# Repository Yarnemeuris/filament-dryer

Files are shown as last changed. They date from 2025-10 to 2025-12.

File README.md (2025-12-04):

# filament-dryer
A simple filament dryer for drying 1 kg spools of filament. It's based around an Ender 3 heater and fan, combined with a PCB and another sensor. All controlled via Klipper. More information on CAD, firmware and the PCB is available in the folders.

CAD model

## CAD
The filament is made for 3D printing and it will use about 350g of ABS/ASA. I deigned it in onshape, here is the [link](https://cad.onshape.com/documents/1bd024d5b7959acafc85207a/w/bc3f431890b8dcf2703dc2b2/e/cdbebe0165cb72dab1a66bad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) if you want to see it yourself. Here are some more pictures from onshape:

electronics
side view
open

## PCB
It uses a custom 2 layer pcb, that's designed to be hand soldered. Most of the components are through hole and the one that isn't is pretty zasy to do yourself. Here are some pictures of the pcb:

PCB 3D model
PCB
schematic

## BOM
In the BOM it uses a pico W because that is the only one LCSC has. You could also use a normal pico, but then you will need to get it from somewhere else.

| Category | Item | Quantity | Minimum Order Quantity | Unit Price | Total Price | URL | Running Total |
| ---: | ---: | ---: | ---: | ---: | ---: | ---: | ---: |
| PCB Components | Capacitor 10µF | 1 | 1 |  $ 0.3996  | $0.40 | https://www.lcsc.com/product-detail/C531341.html |  $ 0.40  |
| PCB Components | Capacitor 22µF | 1 | 1 |  $ 1.2269  | $1.23 | https://www.lcsc.com/product-detail/C531341.html |  $ 1.63  |
| PCB Components | JST XH connector | 5 | 10 |  $ 0.0482  | $0.48 | https://www.lcsc.com/product-detail/C378939.html |  $ 2.11  |
| PCB Components | Screw Terminal | 2 | 5 |  $ 0.1102  | $0.55 | https://www.lcsc.com/product-detail/C8465.html |  $ 2.66  |
| PCB Components | Mosfet | 2 | 1 |  $ 0.8775  | $1.76 | https://www.lcsc.com/product-detail/C38774.html |  $ 4.41  |
| PCB Components | Resistor 100Ω | 2 | 50 |  $ 0.0110  | $0.55 | https://www.lcsc.com/product-detail/C120214.html |  $ 4.96  |
| PCB Components | Resistor 100KΩ | 2 | 20 |  $ 0.0242  | $0.48 | https://www.lcsc.com/product-detail/C119444.html |  $ 5.45  |
| PCB Components | Resistor 120Ω | 1 | 20 |  $ 0.0122  | $0.24 | https://www.lcsc.com/product-detail/C359996.html |  $ 5.69  |
| PCB Components | Resistor 7KΩ | 1 | 20 |  $ 0.0229  | $0.46 | https://www.lcsc.com/product-detail/C119429.html |  $ 6.15  |
| PCB Components | CAN Transceiver | 1 | 1 |  $ 2.6161  | $2.62 | https://www.lcsc.com/product-detail/C16468.html |  $ 8.77  |
| PCB Components | Voltage Regulator | 1 | 1 |  $ 3.5895  | $3.59 | https://www.lcsc.com/product-detail/C22371890.html |  $ 12.36  |
| PCB Components | Jumper | 1 | 5 |  $ 0.0880  | $0.44 | https://www.lcsc.com/product-detail/C265313.html |  $ 12.80  |
| PCB Components | AHT21 Sensor | 1 | 1 |  $ 1.5105  | $1.51 | https://www.lcsc.com/product-detail/C3012624.html |  $ 14.31  |
| PCB Components | Pico W | 1 | 1 |  $ 10.7204  | $10.72 | https://www.lcsc.com/product-detail/C7203003.html |  $ 25.03  |
| PCB Components | 1x20 Pin Header | 2 | 5 |  $ 0.0566  | $0.28 | https://www.lcsc.com/product-detail/C42431804.html |  $ 25.31  |
| PCB Components | LCSC Shipping lcsc shipping | 1 |  |  $ 10.88  | $10.88 |  |  $ 36.19  |
| PCB | PCB (incl. shipping) jlcpcb shipping | 1 | 1 |  $ 4.24  | $4.24 | https://jlcpcb.com/ |  $ 40.43  |
| Parts | Heater | 1 |  | (from Ender 3) |  |  |  $ 40.43  |
| Parts | 4010 Blower Fan | 1 |  | (from Ender 3) |  |  |  $ 40.43  |
| Case | Printed Parts | 350g |  |  (I already own)  |  |  |  $ 40.43  |
| Case | Screws M3x12 | 4 |  |  (I already own)  |  |  |  $ 40.43  |
| Case | Screws M3x8 | 2 |  |  (I already own)  |  |  |  $ 40.43  |
| Case | Screws M3x16 | 2 |  |  (I already own)  |  |  |  $ 40.43  |
| Case | M3 Nuts | 6 |  |  (I already own)  |  |  |  $ 40.43  |
| Case | voron inserts | 2 |  |  (I already own)  |  |  |  $ 40.43  |

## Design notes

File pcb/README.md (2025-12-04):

# PCB
The filament dryer uses a custom 2 layer pcb. I made it with almost only through hole components, so you don't need to order PCBA. But make sure when you order on both JLCPCB and LCSC that you chose global standard direct line. It is the cheapest option and bad things will happend if you don't. All the files needed for the pcb production and parts are in de production folder. The zip is the gerber files for JLCPCB and you can upload the bom.csv to LCSC. But add the extra sensor, pico and headers to your cart as well.

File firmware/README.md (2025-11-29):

# Firmware

Here you can find the Klipper config. The firmware for the Pico itself can be obtained via Klipper itself. It should have the default settings, but communication is via CANbus with RX on pin 4 and TX on pin 5.

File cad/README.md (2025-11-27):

# CAD
There is a step file with the whole filament dryer in it, including the PCB and not printed components. You can also visit the [Onshape document](https://cad.onshape.com/documents/1bd024d5b7959acafc85207a/w/bc3f431890b8dcf2703dc2b2/e/cdbebe0165cb72dab1a66bad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), to view it and how I made it for yourself.

I have also included an STL file for each part to print. Which are orientated how I think you should print them (some have long bridges).

Lastly, there is also an OrcaSlicer 3MF file with the exact settings I used to print it.

## Print Settings
I don't have much to say here. I would recommend printing it from ABS or ASA, because it will get hot and PLA will melt. I used settings that aren't very strong but save filament. But it still is like 400 g.

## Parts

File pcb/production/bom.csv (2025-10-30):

Designator | Footprint | Quantity | Value | LCSC Part #
A1 | RaspberryPi_Pico_Common_THT | 1 | RaspberryPi_Pico
C1 | C_Disc_D6.0mm_W4.4mm_P5.00mm | 1 | 10µF | C531341
C2 | C_Disc_D6.0mm_W4.4mm_P5.00mm | 1 | 22µF | C5259863
J1, J3, J4, J5, J7 | JST_XH_B2B-XH-A_1x02_P2.50mm_Vertical | 5 | Conn_01x02 | C378939
J2, J6 | TerminalBlock_CUI_TB007-508-02_1x02_P5.08mm_Horizontal | 2 | Screw_Terminal | C8465
Q1, Q2 | TO-220-3_Horizontal_TabDown | 2 | IRLZ44N | C38774
R1, R2 | R_Axial_DIN0309_L9.0mm_D3.2mm_P12.70mm_Horizontal | 2 | 100Ω | C120214
R3, R4 | R_Axial_DIN0309_L9.0mm_D3.2mm_P12.70mm_Horizontal | 2 | 100KΩ | C119444
R6 | R_Axial_DIN0309_L9.0mm_D3.2mm_P12.70mm_Horizontal | 1 | 120Ω | C359996
R7 | R_Axial_DIN0309_L9.0mm_D3.2mm_P12.70mm_Horizontal | 1 | 4.7KΩ | C119429
U1 | SOIC-8_3.9x4.9mm_P1.27mm | 1 | SN65HVD230 | C16468
U2 | Converter_DCDC_RECOM_R-78E-0.5_THT | 1 | R-78E5.0-1.0 | C22371890

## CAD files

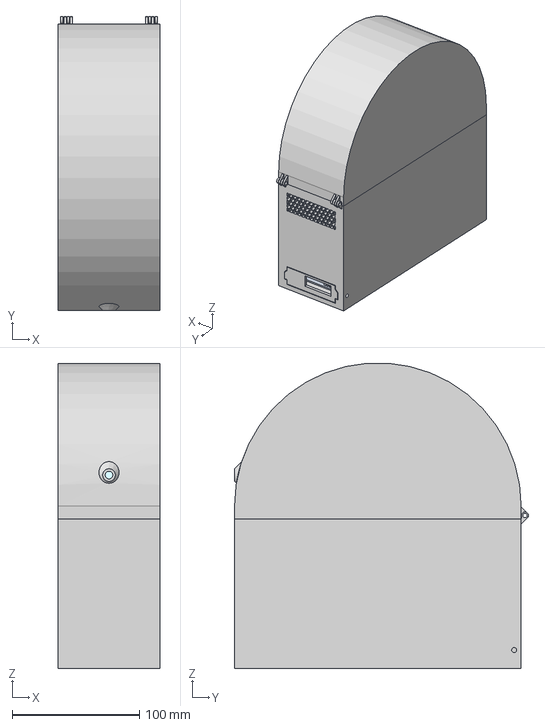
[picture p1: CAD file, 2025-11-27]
cad/filament dryer.step
80.0 x 230.7 x 239.7 mm

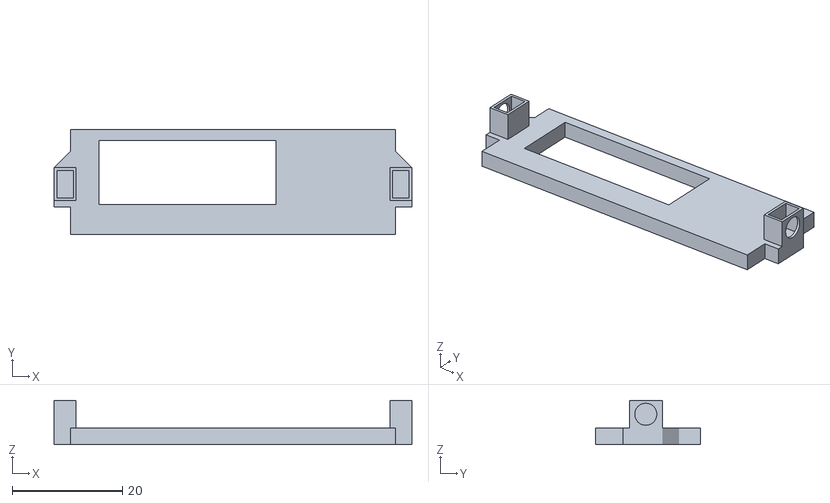
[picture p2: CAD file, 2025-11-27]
cad/STLs/backdoor.stl
65.0 x 19.0 x 8.00

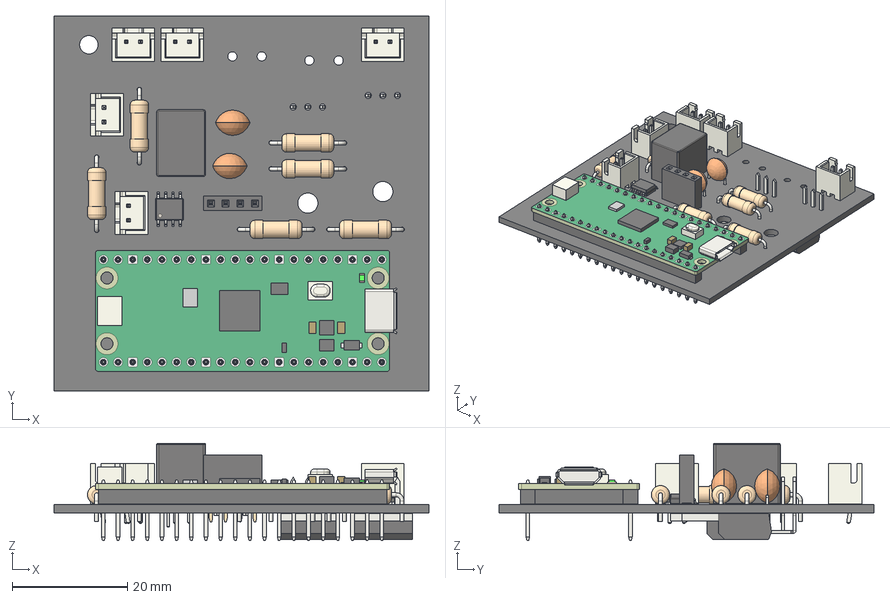
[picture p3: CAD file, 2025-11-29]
pcb/filament dryer.step
65.0 x 65.0 x 16.9 mm
C_Disc_D6.0mm_W4.4mm_P5.00mm x 2
SOIC-8_3.9x4.9mm_P1.27mm
R_Axial_DIN0309_L9.0mm_D3.2mm_P12.70mm_Horizontal x 6
JST_XH_B2B-XH-A_1x02_P2.50mm_Vertical x 5
RaspberryPi_Pico_H_Module_KiCad
RaspberryPi_Pico_Header_DIP-40_H2.54mm_KiCad
PinSocket_1x04_P2.54mm_Vertical
Converter_DCDC_RECOM_R-78E-0.5_THT
TO-220-3_Horizontal_TabDown x 2
filament dryer_PCB

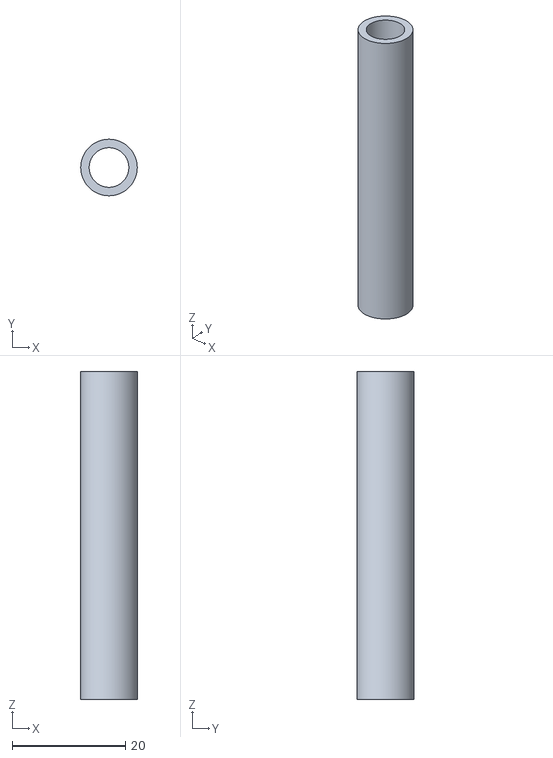
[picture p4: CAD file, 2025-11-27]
cad/STLs/2x_roller.stl
10.00 x 10.00 x 58.0

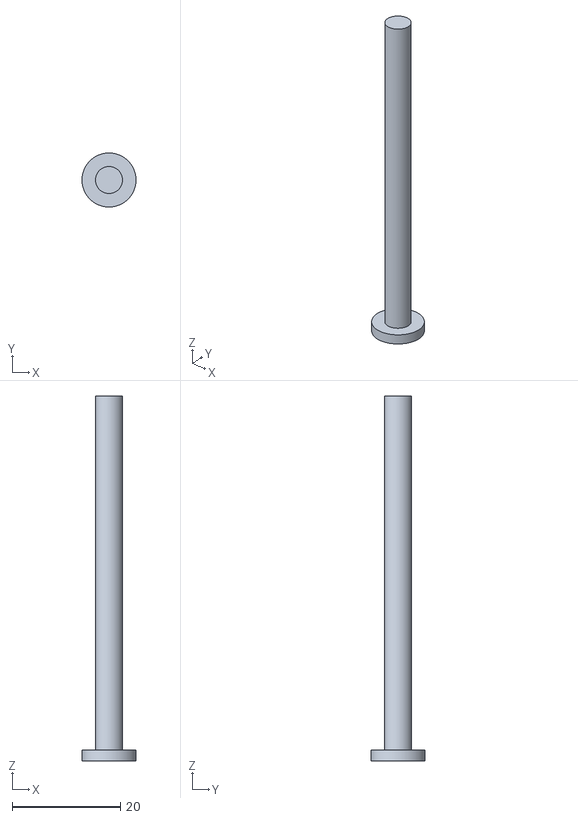
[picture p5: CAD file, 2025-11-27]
cad/STLs/2x_roller_pin.stl
10.00 x 10.00 x 67.5

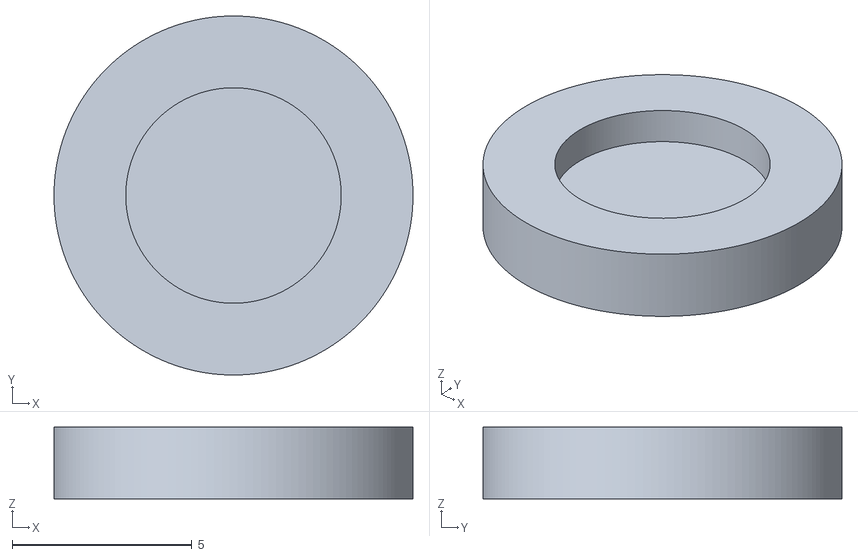
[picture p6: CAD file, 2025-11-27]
cad/STLs/2x_roller_cap.stl
10.00 x 10.00 x 2.00

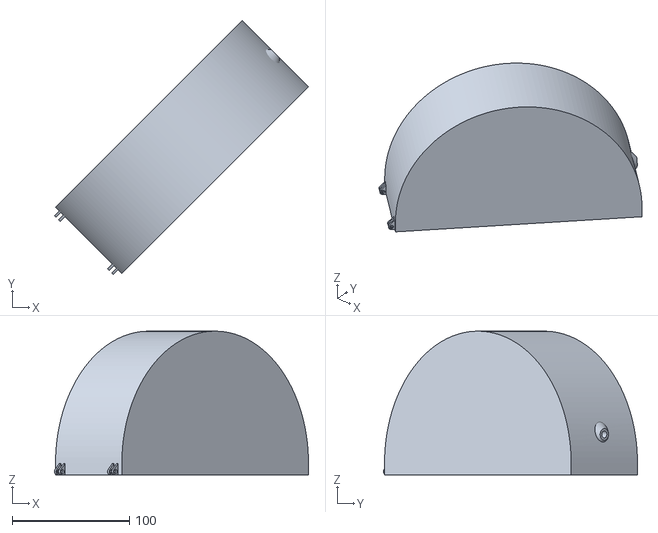
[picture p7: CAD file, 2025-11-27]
cad/STLs/top.stl
216.5 x 216.5 x 122.5

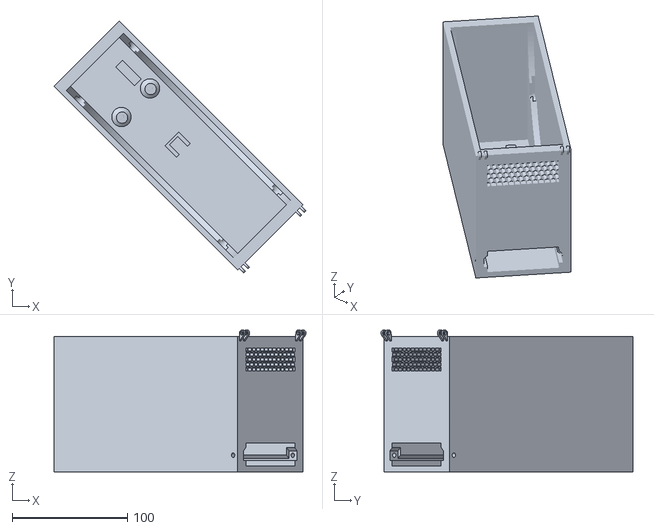
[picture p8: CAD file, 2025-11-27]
cad/STLs/bottom.stl
218.3 x 218.3 x 123.0

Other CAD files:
cad/filament dryer.3mf

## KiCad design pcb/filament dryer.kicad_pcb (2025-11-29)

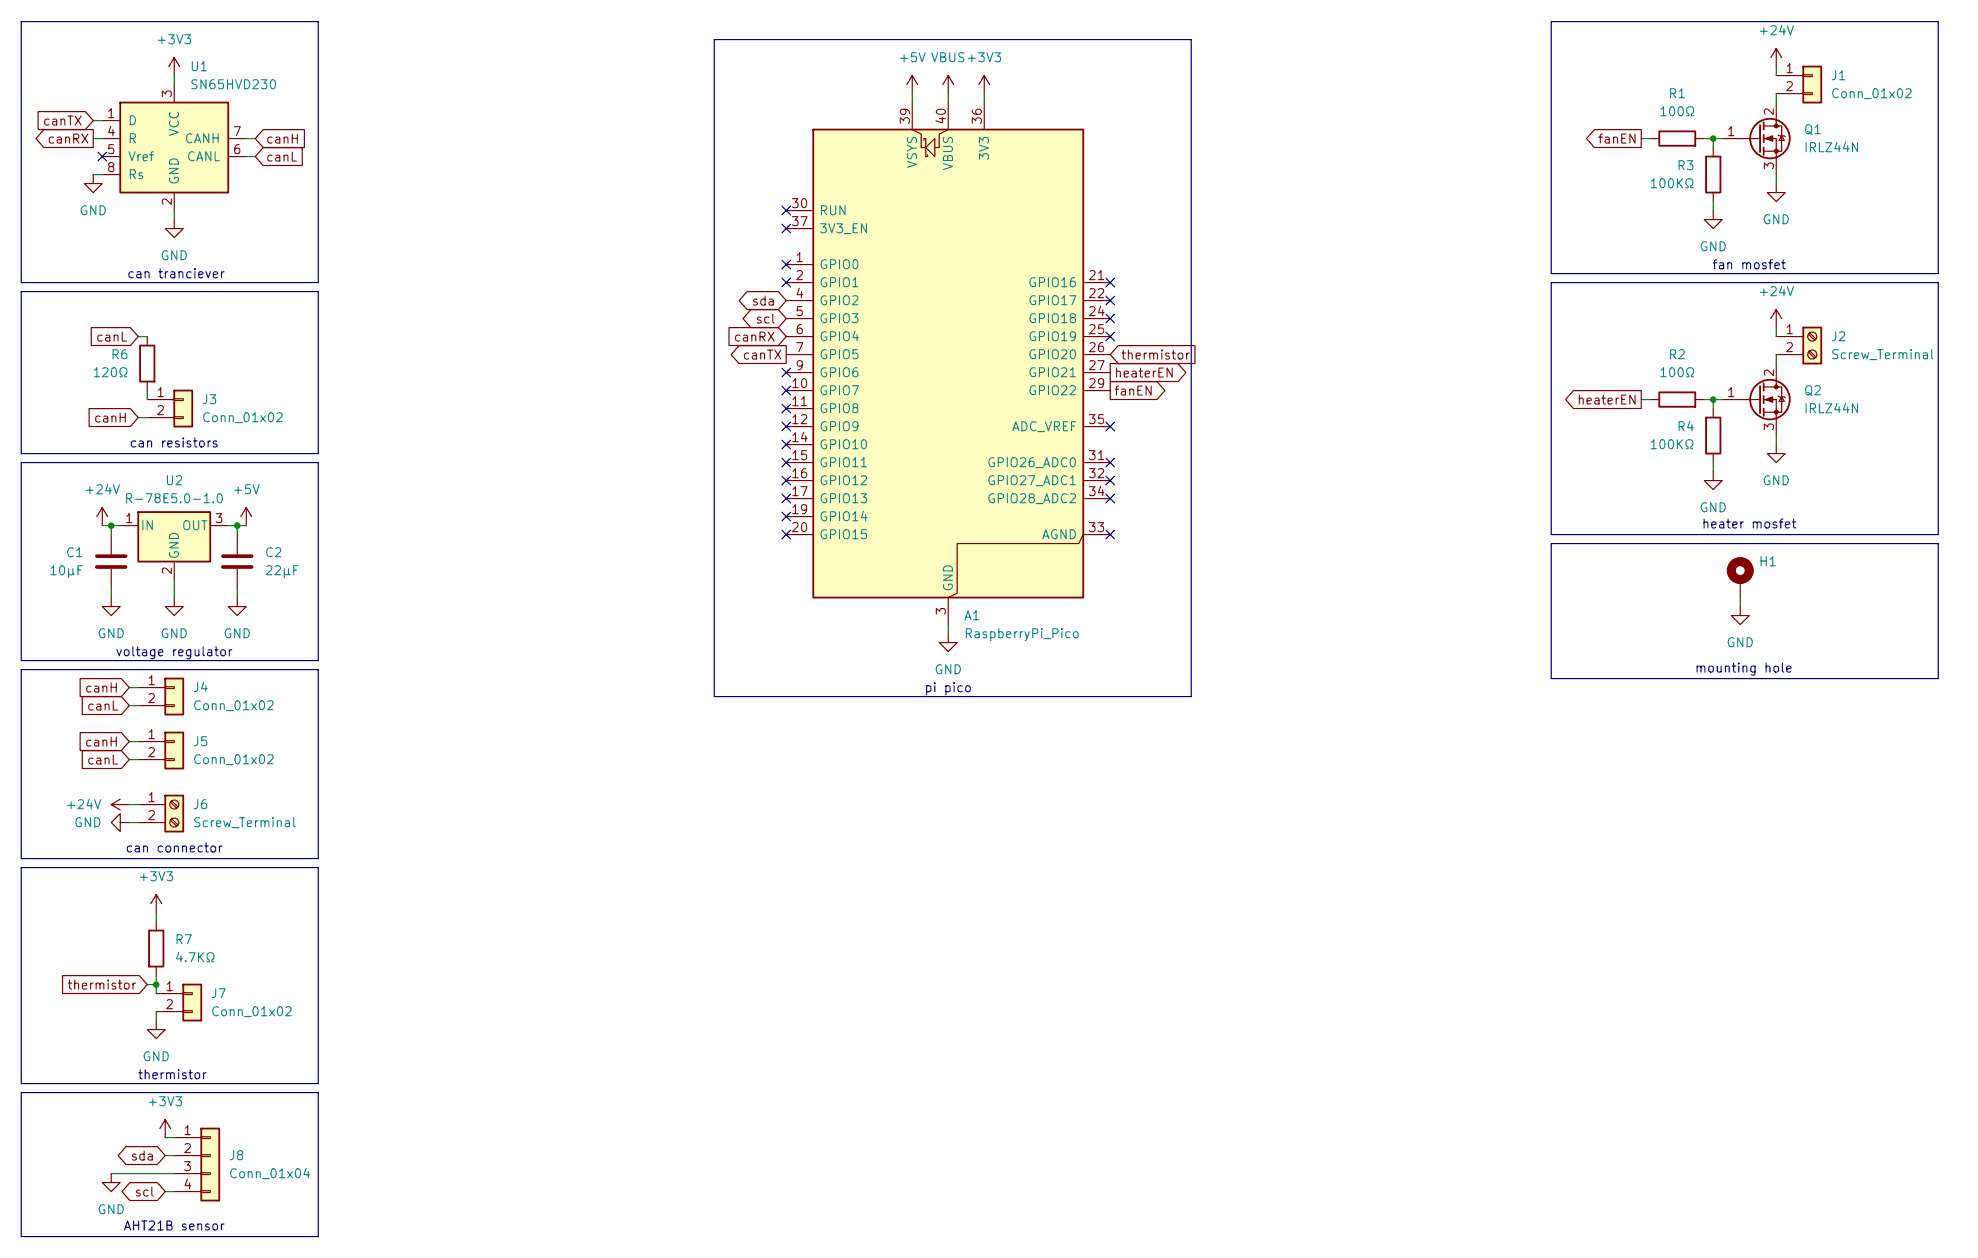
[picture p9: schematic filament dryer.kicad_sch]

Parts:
A1: RaspberryPi_Pico; RaspberryPi_Pico_Common_THT
C1: 10µF; C_Disc_D6.0mm_W4.4mm_P5.00mm; LCSC Part C531341
C2: 22µF; C_Disc_D6.0mm_W4.4mm_P5.00mm; LCSC Part C5259863
H1: MountingHole; MountingHole_3.2mm_M3_Pad
J1, J3, J4, J5, J7: Conn_01x02; JST_XH_B2B-XH-A_1x02_P2.50mm_Vertical; LCSC Part C378939
J2, J6: Screw_Terminal; TerminalBlock_CUI_TB007-508-02_1x02_P5.08mm_Horizontal; LCSC Part C8465
J8: Conn_01x04; PinSocket_1x04_P2.54mm_Vertical
Q1, Q2: IRLZ44N; TO-220-3_Horizontal_TabDown; LCSC Part C38774
R1, R2: 100Ω; R_Axial_DIN0309_L9.0mm_D3.2mm_P12.70mm_Horizontal; LCSC Part C120214
R3, R4: 100KΩ; R_Axial_DIN0309_L9.0mm_D3.2mm_P12.70mm_Horizontal; LCSC Part C119444
R6: 120Ω; R_Axial_DIN0309_L9.0mm_D3.2mm_P12.70mm_Horizontal; LCSC Part C359996
R7: 4.7KΩ; R_Axial_DIN0309_L9.0mm_D3.2mm_P12.70mm_Horizontal; LCSC Part C119429
U1: SN65HVD230; SOIC-8_3.9x4.9mm_P1.27mm; LCSC Part C16468
U2: R-78E5.0-1.0; Converter_DCDC_RECOM_R-78E-0.5_THT; LCSC Part C22371890

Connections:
+3V3: A1.36 (3V3), J8.1, R7.1, U1.3 (VCC)
+5V: A1.39 (VSYS), C2.1, U2.3 (OUT)
+24V: C1.1, J1.1, J2.1, J6.1, U2.1 (IN)
GND: A1.3 (GND), A1.8 (GND), A1.13 (GND), A1.18 (GND), A1.23 (GND), A1.28 (GND), A1.38 (GND), C1.2, C2.2, H1.1, J6.2, J7.2, J8.3, Q1.3 (S), Q2.3 (S), R3.1, R4.1, U1.2 (GND), U1.8 (Rs), U2.2 (GND)
unnamed: J1.2, Q1.2 (D)
unnamed: J2.2, Q2.2 (D)
unnamed: J3.1, R6.2
unnamed: Q1.1 (G), R1.2, R3.2
unnamed: Q2.1 (G), R2.2, R4.2
VBUS: A1.40 (VBUS)
canH: J3.2, J4.1, J5.1, U1.7 (CANH)
canL: J4.2, J5.2, R6.1, U1.6 (CANL)
canRX: A1.6 (GPIO4), U1.4 (R)
canTX: A1.7 (GPIO5), U1.1 (D)
fanEN: A1.29 (GPIO22), R1.1
heaterEN: A1.27 (GPIO21), R2.1
scl: A1.5 (GPIO3), J8.4
sda: A1.4 (GPIO2), J8.2
thermistor: A1.26 (GPIO20), J7.1, R7.2

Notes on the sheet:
fan mosfet
voltage regulator
can connector
heater mosfet
can tranciever
mounting hole
pi pico
can resistors
AHT21B sensor
thermistor

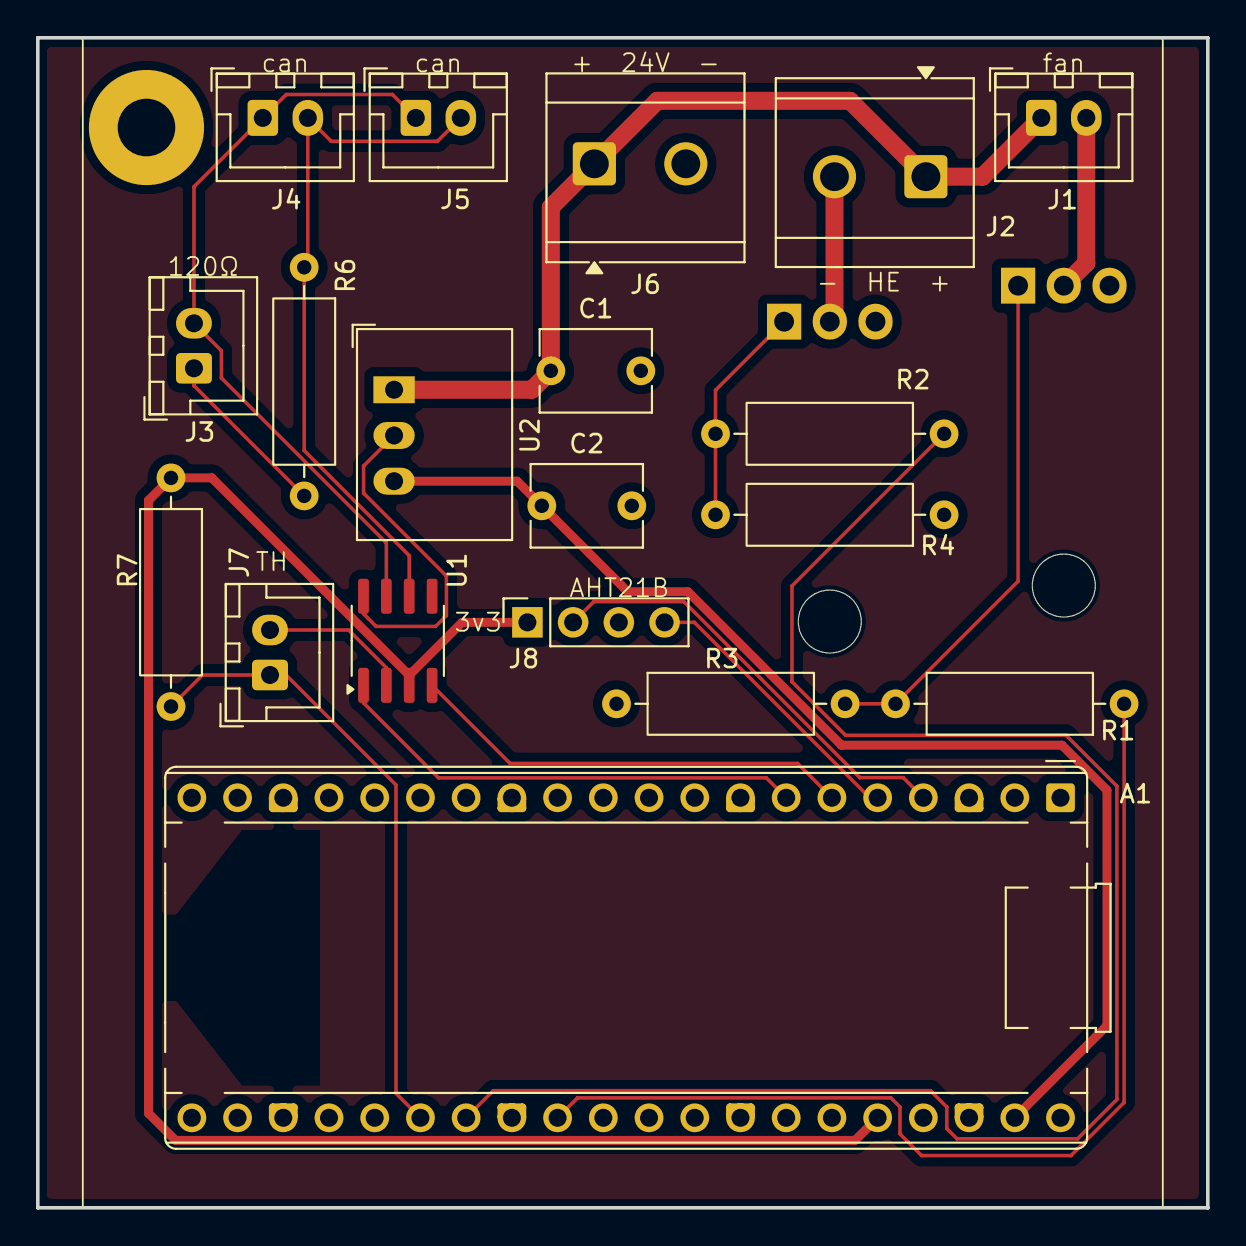
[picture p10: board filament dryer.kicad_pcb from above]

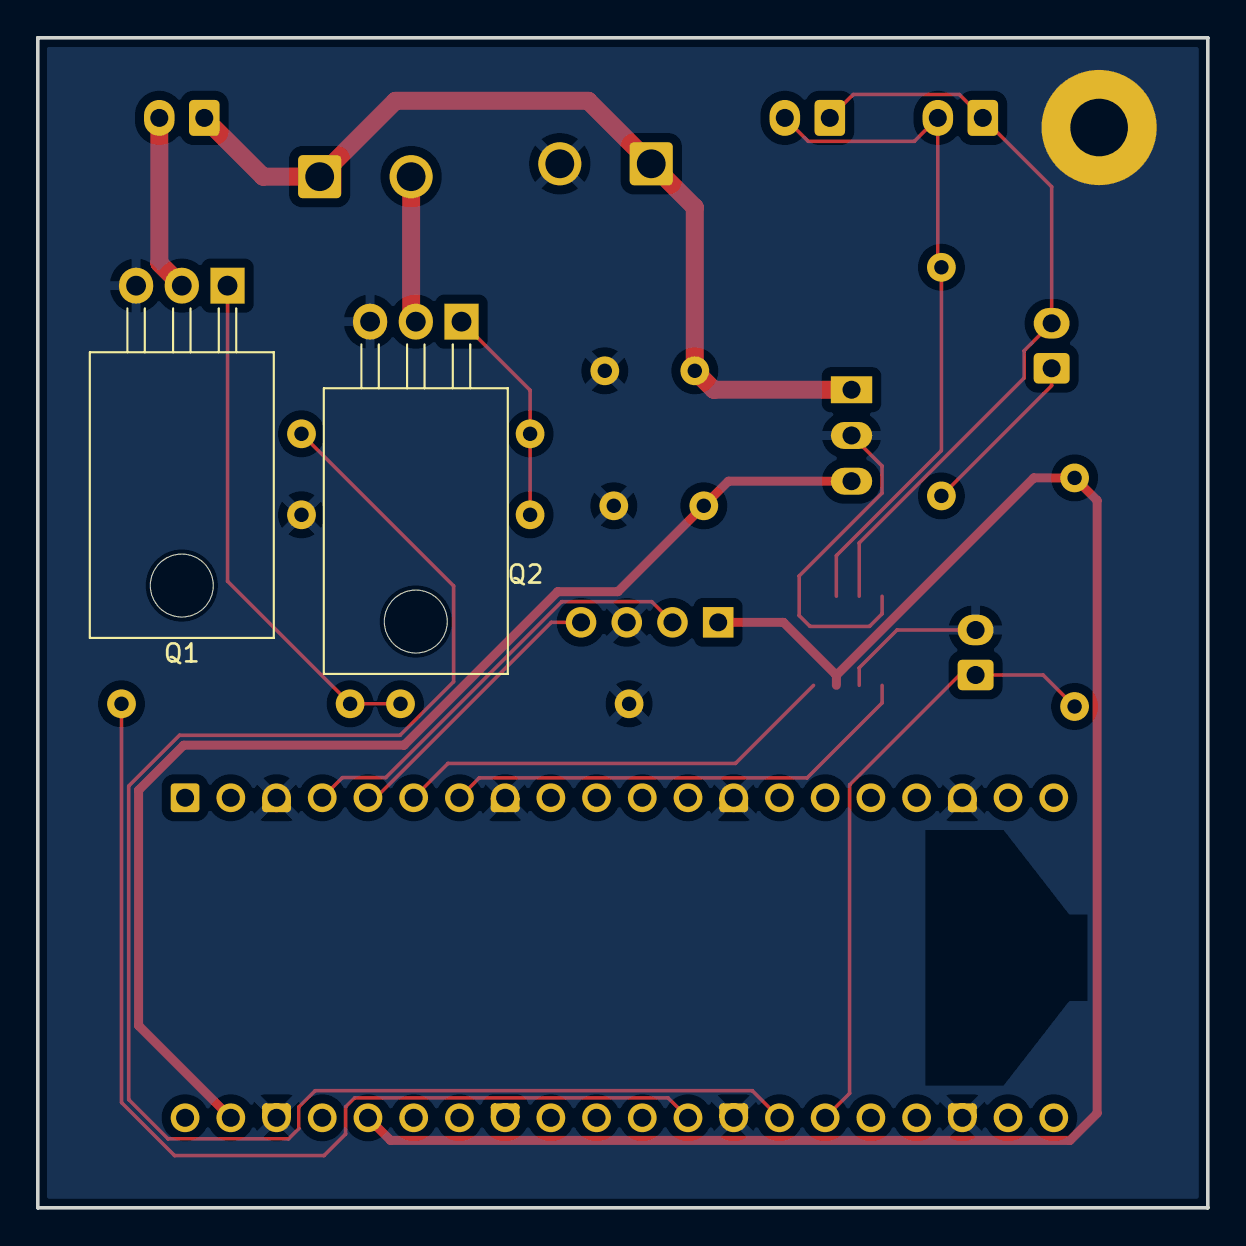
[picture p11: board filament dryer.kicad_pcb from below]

Board: 2 copper layers, 65.0 x 65.0 mm, 22 parts (2 on the bottom side), 18 nets.

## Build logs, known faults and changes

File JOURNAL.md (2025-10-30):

<!--
  ===================    !!READ THIS NOTICE!!   ====================
  DO NOT edit this file manually. Your changes WILL BE OVERWRITTEN!
  This journal is auto generated and updated by Hack Club Blueprint.
  To edit this file, please edit your journal entries on Blueprint.
  ==================================================================
-->

## 10/26/2025 - Made the schematic  

So this is the first day I'm working on this, but I had been thinking about it for some time. So it wasn't very difficult to make the schematic.



It's also not that complicated and I think I have everything. I also started working on the pcb.



I almost have the first version but it will change a lot while I'm making the model.  

## 10/29/2025 - worked on the schematic and pcb  

I forgot to add the thermistor connectors to the schematic and pcb. So I did that along with changing some components so that there are less different components. This is what the pcb looks like now.



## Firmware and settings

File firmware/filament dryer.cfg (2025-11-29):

[mcu filament_dryer]
canbus_uuid: #Put your actual can uuid
restart_method: command

[heater_generic filament_dryer_heater]
gcode_id: filament_dryer
heater_pin: filament_dryer:gpio21
control: watermark
sensor_type: EPCOS 100K B57560G104F
sensor_pin: filament_dryer:gpio20
min_temp: 0
max_temp: 80

[heater_fan filament_dryer_fan]
pin: filament_dryer:gpio22
heater: filament_dryer_heater
heater_temp: 35.0

[temperature_sensor filament_dryer_sensor]
sensor_type: AHT10
i2c_mcu: filament_dryer

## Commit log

2025-11-27 PCB/CAD with README's
    [2x_roller.stl, 2x_roller_cap.stl, 2x_roller_pin.stl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]
2025-11-29 pcb update and firmware
    [filament dryer.cfg, filament dryer.kicad_pcb, filament dryer.kicad_sch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]
2025-11-30 Added the BOM
    [BOM.csv]
2025-12-04 Added README for PCB folder
